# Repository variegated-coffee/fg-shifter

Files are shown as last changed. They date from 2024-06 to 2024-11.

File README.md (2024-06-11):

# FG Level Shifter

Fluid-o-tech FG20x/30x/40x gear pumps run at 5V, but Variegated Coffee boards prefer 3V3. The pumps also prefer a smooth control signal. PWM signals aren't. This is a really tiny board designed to fit into a Hammond 1551G project box allowing you to shift between 5V and 3V3, and to add an RC filter to smooth out the PWM signal.

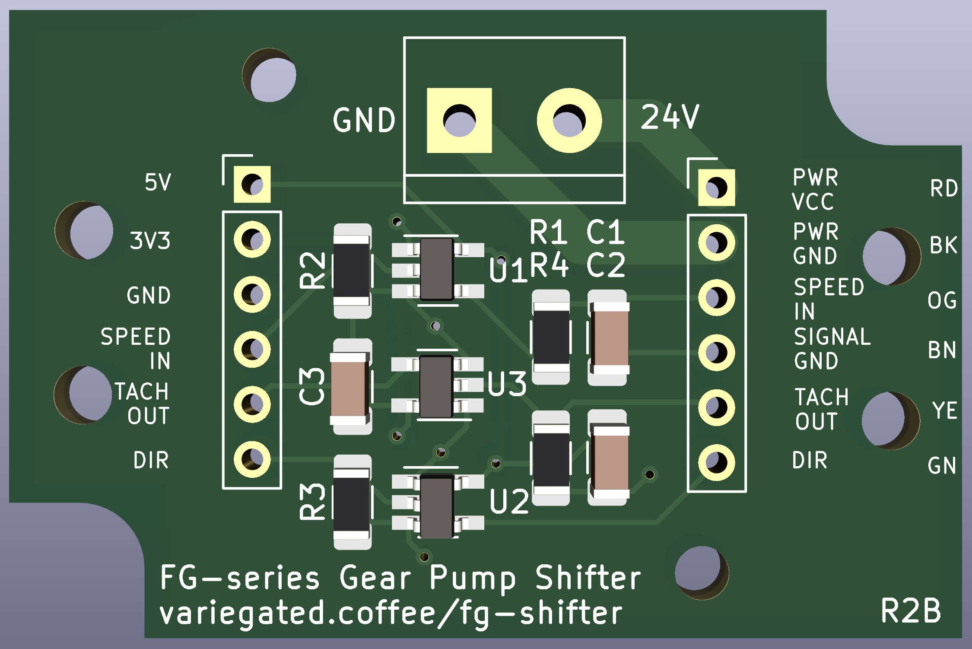
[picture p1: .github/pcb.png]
PCB


*R2B is the current revision, but is yet to be manufactured. You shouldn't be the first to do so.*

## Features

* PCB outline matching a Hammond 1551G project box
* Terminal block for 24V power
* Connection to pump and to the controller can use either a terminal block, or something like a right-angled JST-XH connector
* 1206 and SOT-23-5 components for relatively easy hand soldering
* Extra holes for adding zip ties as strain relief

## Cabling

If you open up a FG series pump, you'll find the the stock cable is attached using a connector. That connector is a TE AMP CT 6 position connector (2.00 mm pitch). If you're unhappy with the stock cable, you should be able to create a new one.

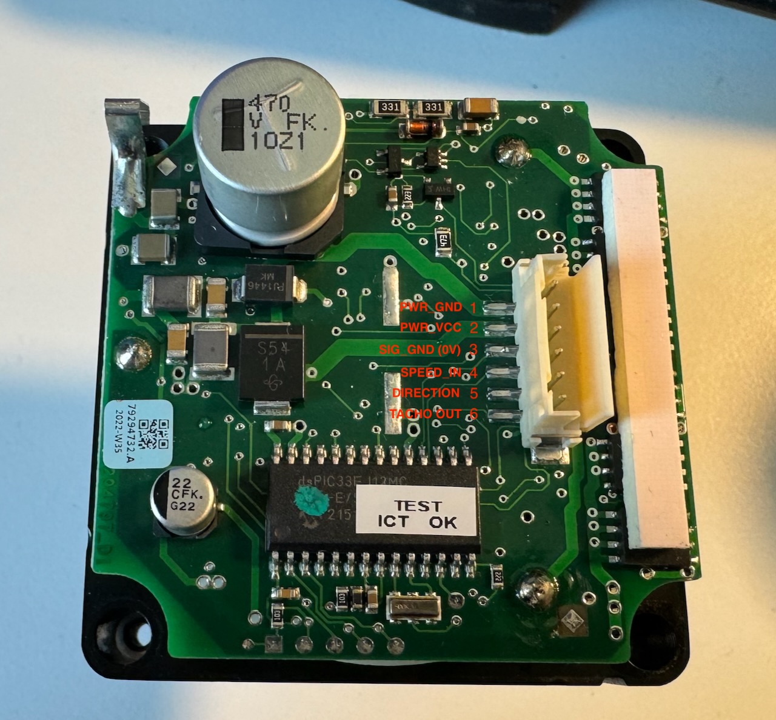
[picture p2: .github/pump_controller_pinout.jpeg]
Pump controller board pinout


## Changelog

* R1A -> R1B
  * Fixed hole positions
* R1B -> R2A 
  * Changed the board to not just be an RC filter, but to also do level shifting
* R2A -> R2B
  * Added bypass caps and Variegated coffee logo
  * Changed pinouts on connectors, to keep optional pins towards one edge

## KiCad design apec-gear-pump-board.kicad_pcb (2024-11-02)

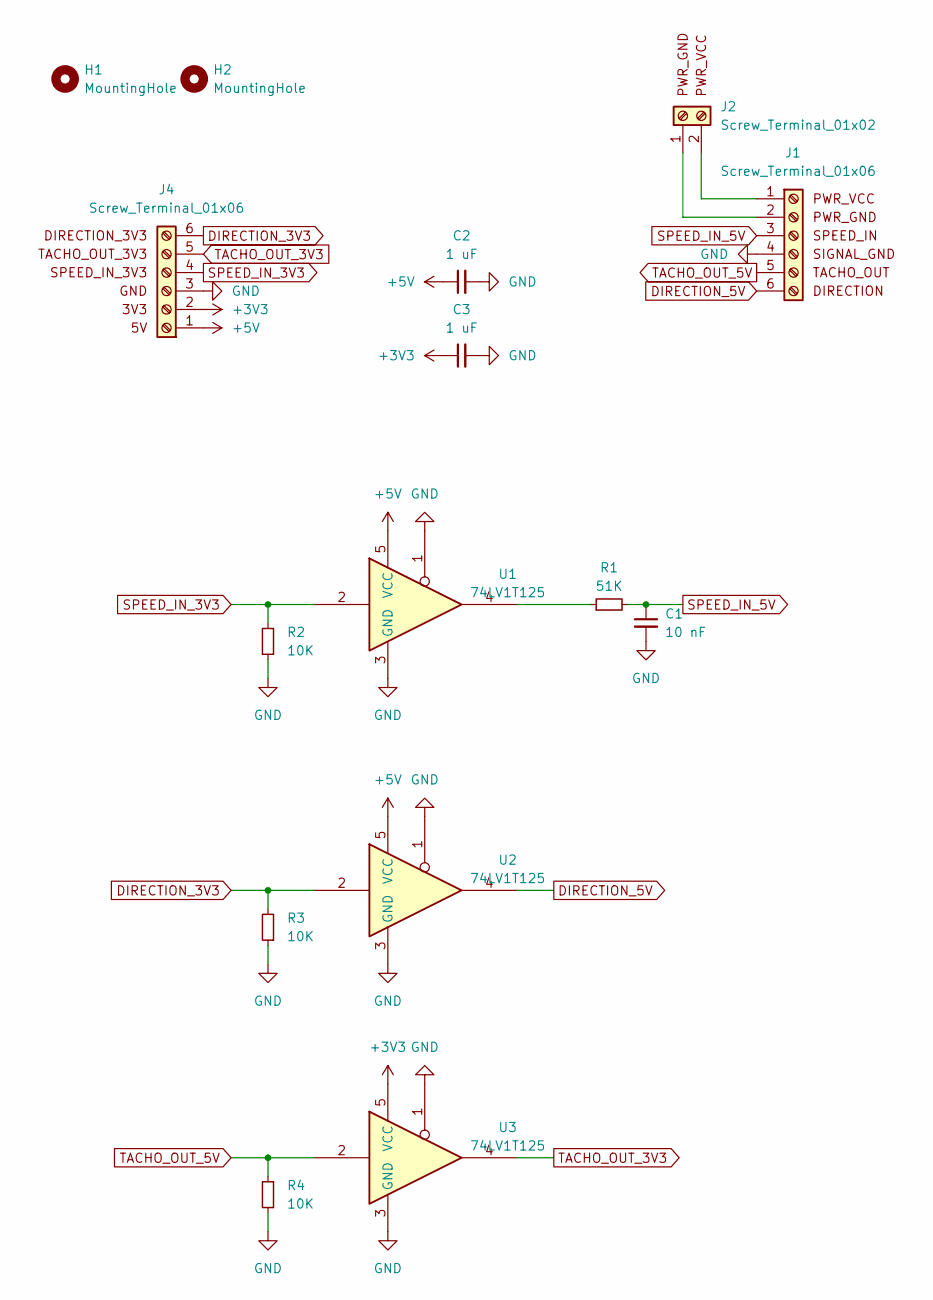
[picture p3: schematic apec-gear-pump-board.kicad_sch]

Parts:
C1: 10 nF; C_1206_3216Metric_Pad1.33x1.80mm_HandSolder; LCSC C1846
C2, C3: 1 uF; C_1206_3216Metric_Pad1.33x1.80mm_HandSolder; Digikey 1276-1068
H1, H2: MountingHole; MountingHole_2.5mm
J1, J4: Screw_Terminal_01x06; PinHeader_1x06_P2.54mm_Vertical
J2: Screw_Terminal_01x02; TerminalBlock_bornier-2_P5.08mm
R1: 51K; R_1206_3216Metric_Pad1.30x1.75mm_HandSolder; LCSC C17992
R2, R3, R4: 10K; R_1206_3216Metric_Pad1.30x1.75mm_HandSolder; LCSC C17902
U1, U2, U3: 74LV1T125; SOT-23-5_HandSoldering; LCSC C473338

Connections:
+3V3: C3.1, J4.2, U3.5 (VCC)
+5V: C2.1, J4.1, U1.5 (VCC), U2.5 (VCC)
DIRECTION_3V3: J4.6, R3.2, U2.2
DIRECTION_5V: J1.6 (DIRECTION), U2.4
GND: C1.2, C2.2, C3.2, J1.4 (SIGNAL_GND), J4.3, R2.1, R3.1, R4.1, U1.1, U1.3 (GND), U2.1, U2.3 (GND), U3.1, U3.3 (GND)
unnamed: J1.2 (PWR_GND), J2.1 (PWR_GND)
unnamed: J1.1 (PWR_VCC), J2.2 (PWR_VCC)
unnamed: R1.1, U1.4
SPEED_IN_3V3: J4.4, R2.2, U1.2
SPEED_IN_5V: C1.1, J1.3 (SPEED_IN), R1.2
TACHO_OUT_3V3: J4.5, U3.4
TACHO_OUT_5V: J1.5 (TACHO_OUT), R4.2, U3.2

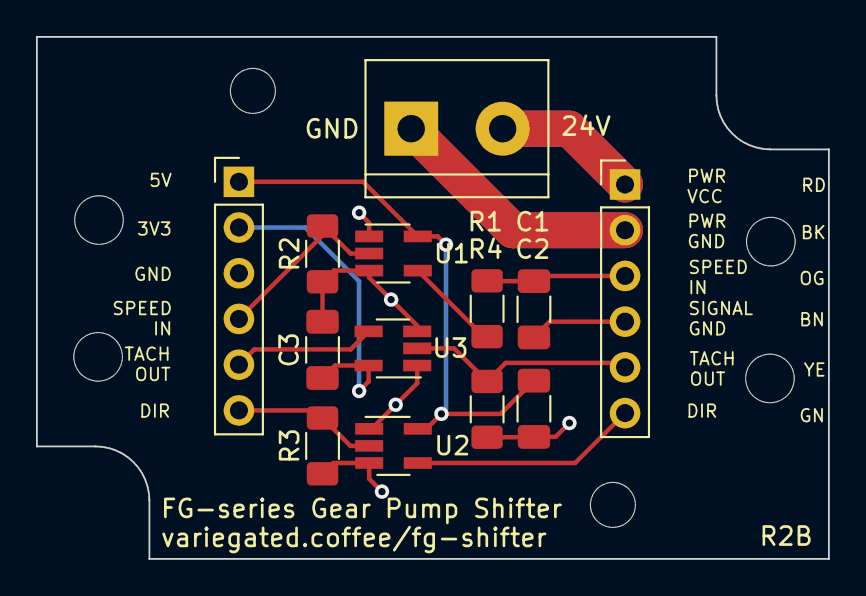
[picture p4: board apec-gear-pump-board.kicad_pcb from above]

Board: 2 copper layers, 44.0 x 29.0 mm, 15 parts (0 on the bottom side), 12 nets.

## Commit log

2024-03-29 Initial import
    [apec-gear-pump-board.kicad_pcb, apec-gear-pump-board.kicad_sch]
2024-03-29 Fixed mistake
    [apec-gear-pump-board.kicad_pcb, apec-gear-pump-board.kicad_sch]
2024-03-30 Cleaned stuff up, and switched to wider tracks for Power
    [apec-gear-pump-board.kicad_pcb, apec-gear-pump-board.kicad_sch]
2024-05-16 Updated the board to do level shifting
    [apec-gear-pump-board.kicad_pcb, apec-gear-pump-board.kicad_sch]
2024-06-01 Added decoupling caps and Variegated Coffee logo
    [apec-gear-pump-board.kicad_pcb, apec-gear-pump-board.kicad_sch]
2024-06-03 More silk screen on the back, changed pinout on the connectors, to put optional pins towards one edge
    [apec-gear-pump-board.kicad_pcb, apec-gear-pump-board.kicad_sch]
2024-11-02 Minor changes
    [apec-gear-pump-board.kicad_pcb]
